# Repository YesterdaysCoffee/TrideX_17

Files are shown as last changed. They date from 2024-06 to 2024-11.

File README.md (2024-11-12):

# TrideX_17
Two headed version of Trident, aka TrideX. Changes include: NEMA 17 steppers for X & Y axis & improved belt assembly.  Generally intended for experienced builders due to lack of step-by-step instructions.  Klipper now supports copy printing for printing two copies at a time, however leveling nozzles can be tricky.  In the future a method to adjust the height of the second head will be added.

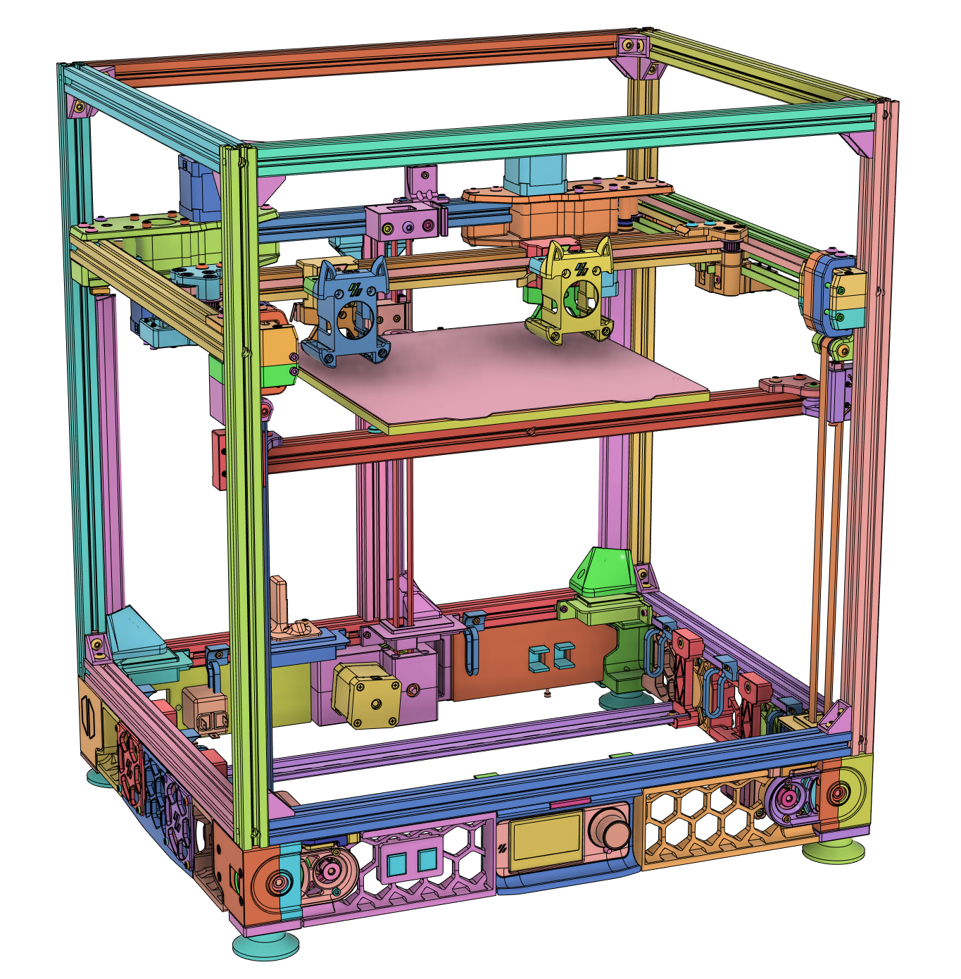
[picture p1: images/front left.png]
Front View.


This is an updated version of TrideX by [eddietheengineer](https://github.com/FrankenVoron/Tridex).

Active development of IDEX macros can be found here: [joseph-greiner's IDEX code](https://github.com/joseph-greiner/tridex_mods/tree/main/printer_configuration)  (as of 2024-7-16).

# Version 0.9
This version uses my favored tool-head, probe, hot-end and end-stop switches.  Depending on popularity and demand, other options can be included (contact me).
Assembly depends on using 3mm and 5mm heat set inserts, some stls have variations using 5mm nuts.  My build used the following and I encourage you to use your favored accessories:
  - Tool-head: Dragon Burner (it is relatively narrow)
  - Bed probe: PCB Klicky, Chartographer 3D being tested
  - Hot-end: Rapido HF, other non-high-flow HE's will likely work
  - End-stops: Mechanical snap switches, Imron D2HW-A201D.
  - Tool-head wiring?  CANbus only (well, maybe USB...)

# 9mm Belts?
Yes, I have started drawing up a gantry using 9mm X/Y belts.  The X linear rail might change.

# Features and Improvements:
  - NEMA 17 steppers for X and Y
  - Belted Z using standard NEMA 17 motors and standard design from VORON Design and MathmaticalPotato, with changes.
  - Improved belt path and belt assembly

# Skirts & Corners:
  - Optional power switch on sides
  - USB port in front skirts
  - LED power switch and dimmer on front skirts, independent from main power switch (warning, I will probably remove this since I was not happy with the results)

  - Electronics bay accessible from the chamber (no more flipping upside down)

# Sizing:
My recommended sizing.  Take your build plate size and:
  - Add 100mm to X (width)
  - Add 50mm to Y (depth)

Typical sizes using square build plates:
  - 200mm, use 250mm sides & 300mm Front/rear, note: electronics bay will be very croweded.
  - 250mm, use 300mm sides & 350mm Front/rear
  - 300mm, use 350mm sides & 400mm Front/rear
  - 350mm, stls have not been included, a 9mm belt version is in the works, and will scale up better.
  - 
A good starting point is a 250mm X 250mm build plate with frame size of 350mm width X 300mm depth.

# Random notes:
- Trident's original Z-drive fits fine, use the original Trident skirts and electronic bay assembly.
- Conversion of a Trident to TrideX-17 has been done. I don't know if the same build plate was used but I'd suggest using a smaller build plate.
- Extra width gives enough space for the idle toolhead to park out if the way.
- Extra depth is needed for the wider X/Y drive assembly and any additional accessories you will use back there. 

In truth any size can be built, it's the skirts which limit frame size options.  Be aware with a very long X-gantry might be problematic.

Frame Size uses standards from Voron Trident: 250, 300 & 350mm with the addition of 400mm for X axis and 200mm on Y axis.  Note, the rear gantry support extrusion is shorter than standard.
Warning: 200mm depth will make fitting electronics a challenge (it didn't work for me).
# Extra Files:
[TridX-17 BOM](https://docs.google.com/spreadsheets/d/e/2PACX-1vSPtPn4Brcn_vidSKCY5Uy1v6KD8oOBtxnAigVPllrFKF_peJibIDPYqSZS3NHdLf7wJWIKfuaN0-26/pubhtml) updated 11-11-2024.

[TridX-17 Change Log](https://docs.google.com/spreadsheets/d/e/2PACX-1vTWaBhZNpjk6NEAdd5VofSHPy5cyr7JOfr-hXRtq54E_nhzI_LgpVOrBIPudIq8-uXfLt_XMnXbr9e0/pubhtml) updated 11-11-2024.

# Notes:
  - Many STL's found here are not compatible with anything else.  The Z-drive, XY-drive assembly and XY joints have all been tweaked for alignment, clearance and assembly.
  - Using a square build plate will be easiest to source.
  - My Firmware files (printer.cfg) are still in development, please depend on [joseph-greiner's IDEX code](https://github.com/joseph-greiner/tridex_mods/tree/main/printer_configuration)
  - Use the CAD file for assembly guidance only, the STL's in the CAD may be out of date.

# To do:
- [] Add folding deck to CAD (piano hinges)
- [] Include detailed description of certain parts, such heat insert size in the BOM
- [] Add assembly tips and tricks
- [] Find micro-adjustable tool-head leveling system

# Got Comments, suggestions, gripes, pizza, praise, flames?  Trolls will be ignored.
Mac McCaskie --> yahoo com (no spaces, you know where to put the punctuation)

Please drop a line if you build this, thanks.

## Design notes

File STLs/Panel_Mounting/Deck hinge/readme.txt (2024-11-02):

Description

Print two halves, slide a 3mm rod in and presto - you have a hinge.

Mix and match lengths to get the desired size.  It's helpful to print in pairs, less confusing that way.

Use double sided tape to attach to surface, VHB tape works well (I think VHB means very high bond, 3M has some and you can find generic VHB).  I don't know if VHB sticks to PLA, let us know in the comments.  VHB works well with ABS.

Optional: Insert a M4 x 4mm machine screw into each end and the hinge pin (that's the 3mm rod) will stay in it's hole.

BOM:

    3mm rod, LOH - 10mm: any metal will work.  I use cheap stainless steel.  I.E. a 60mm hinge will need a 50mm rod.  → LOH = length of hinge.  Tip: A clean end will slide in easier than an end with burrs.
    2 M4 x 4mm screw, any head works fine, IMHO a button head is more aesthetically pleasing.

Settings?  That's pretty much up to you and how strong the hinge needs to be.  A good start point would be:

    Layer: 0.20
    Width: 0.40 
    Walls: 3
    Top & Bottom: 4 

Tip:  Is the rod is too tight? Drill out the holes.  But you say: “I don't have a 3mm drill bit long enough.”  Here's the fix:  Make a D-bit: Get a length of rod and file or grind about 10mm or so flat to the center of the rod.  Try to make the edges you are making sharp, those will be the cutting edges.  The end of the rod will look like a 'D'.  Chuck your new D-bit in a drill and drill that hole out.  Oh, go slow to not heat up the plastic and empty the shavings out often.

https://www.printables.com/model/737250-piano-hinge-expandable-lays-or-hangs-flat-ver2-cor

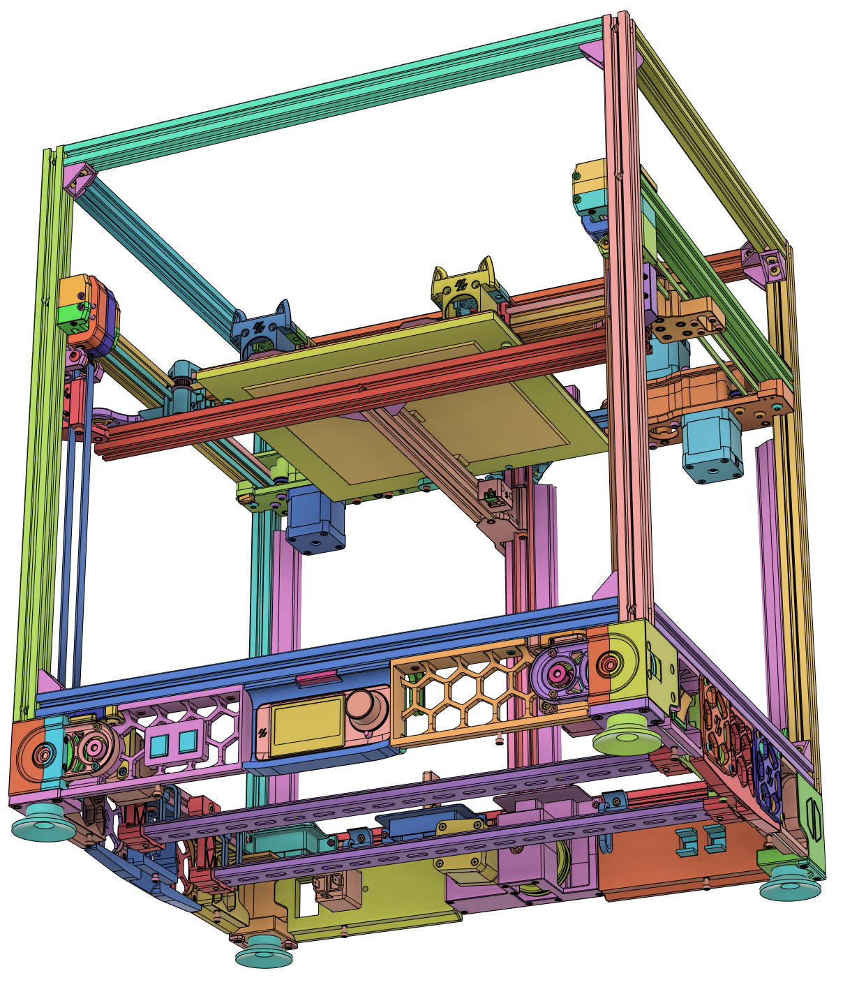
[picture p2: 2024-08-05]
images/front left bottom.png

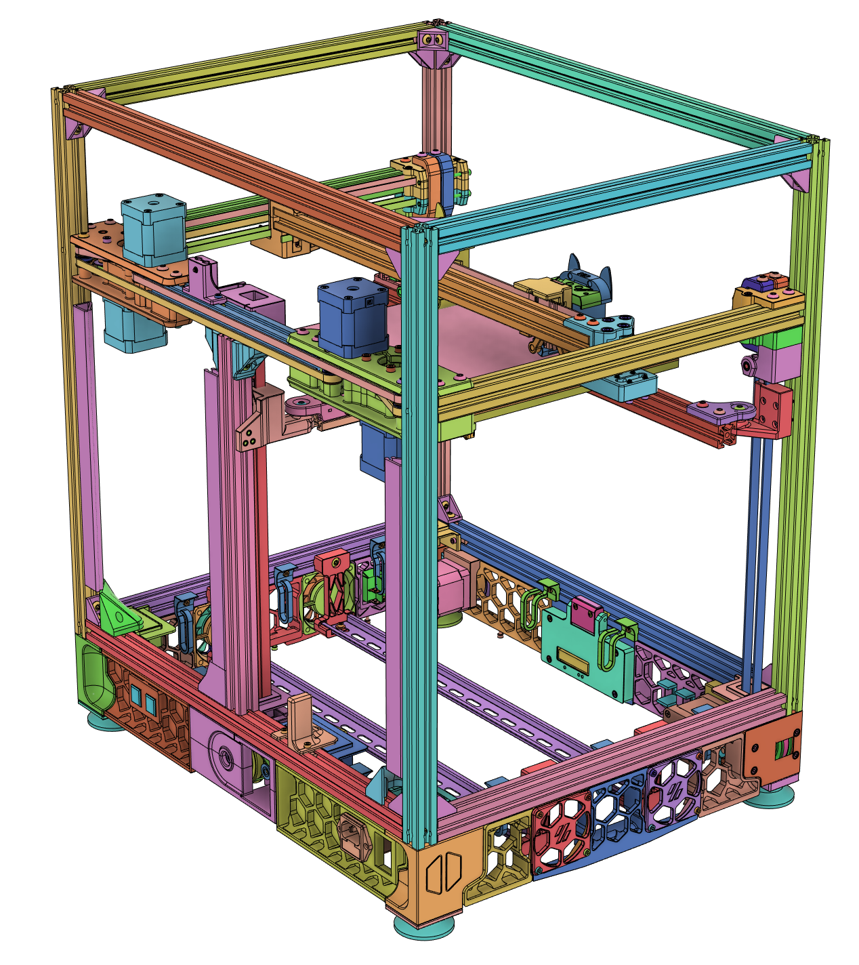
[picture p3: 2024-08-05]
images/back left.png

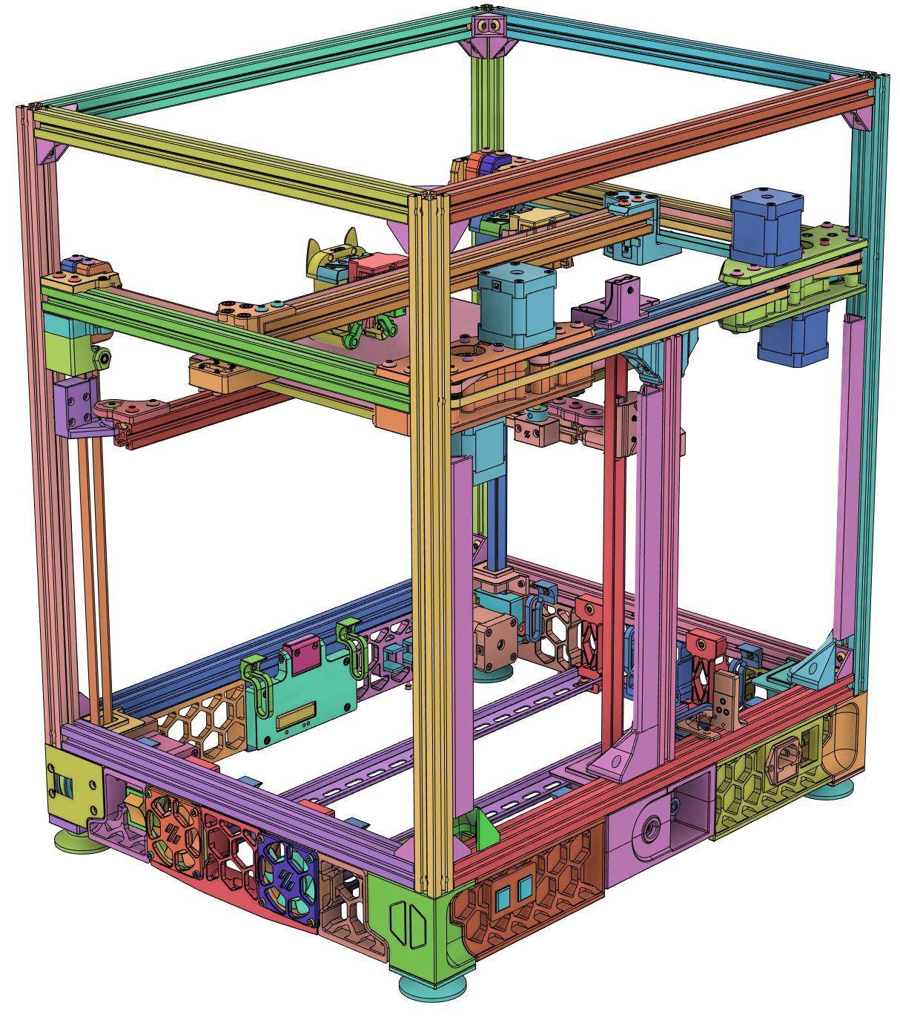
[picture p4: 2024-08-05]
images/front right.png

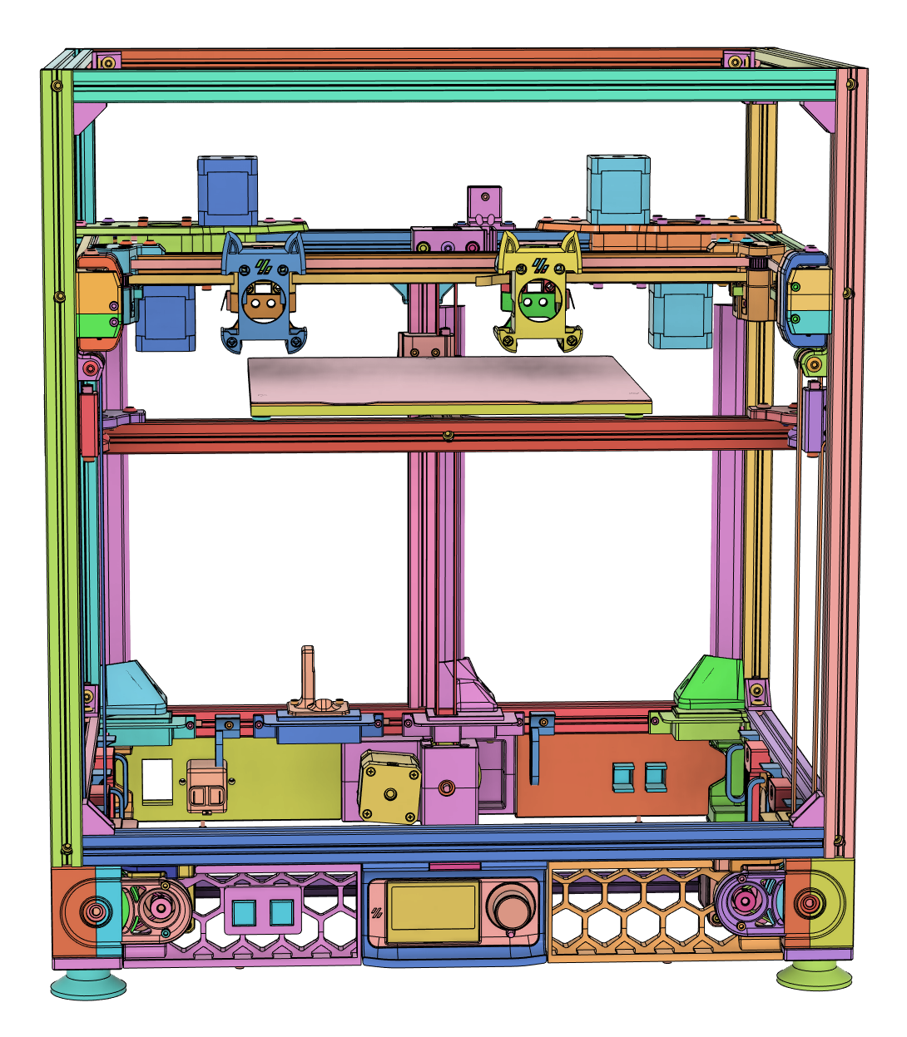
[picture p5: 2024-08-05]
images/front.png

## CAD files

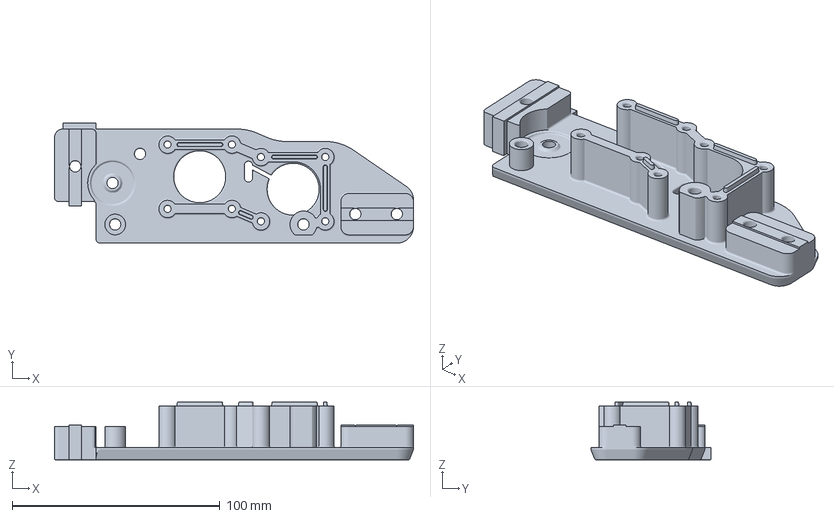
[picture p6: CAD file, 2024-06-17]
STLs/Gantry/XY drive assembly right top/XY drive assembly right bottom.3mf
173.0 x 58.0 x 27.9 mm

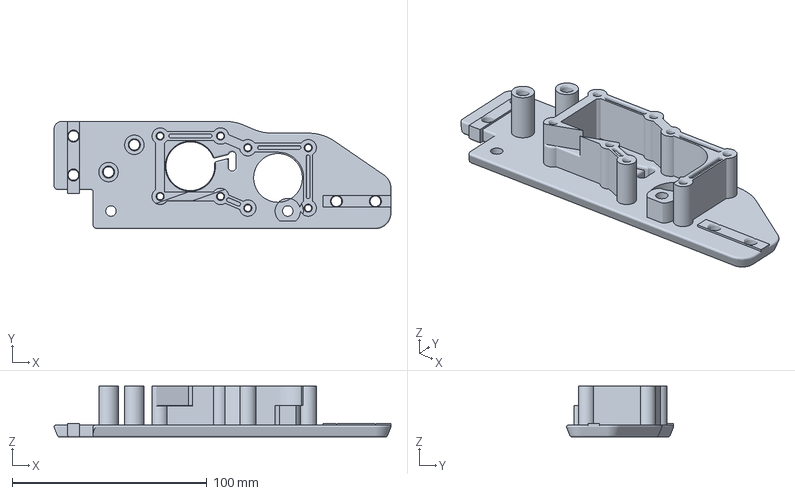
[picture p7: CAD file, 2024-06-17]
STLs/Gantry/XY drive assembly right top/XY drive assembly left top.3mf
173.0 x 55.0 x 26.0 mm

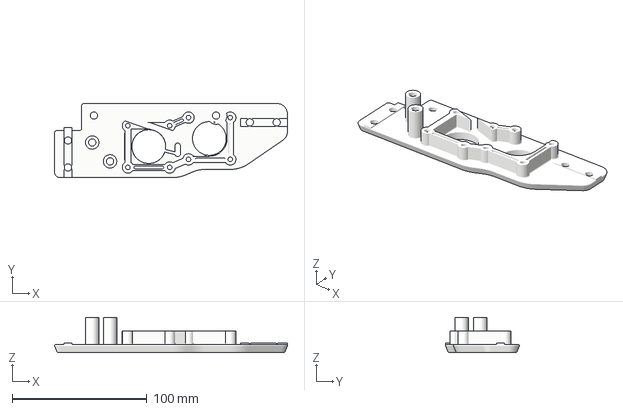
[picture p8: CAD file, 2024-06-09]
STLs/Gantry/XY drive assembly right top/XY drive assembly right top.3mf
173.0 x 55.0 x 26.0 mm

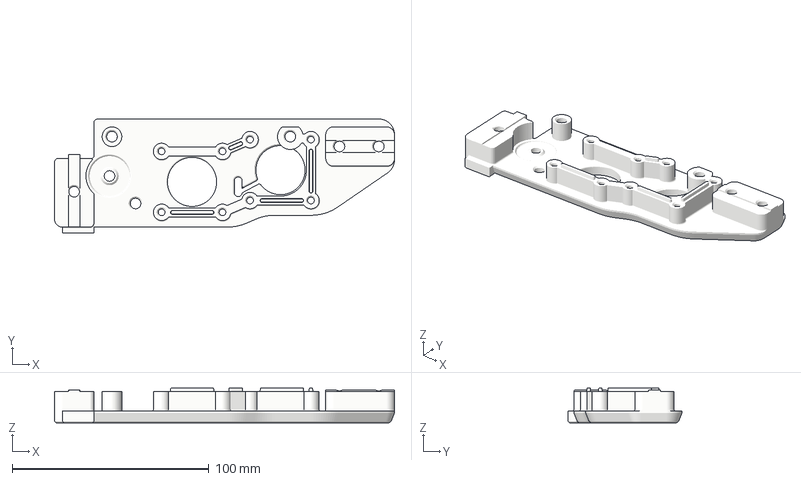
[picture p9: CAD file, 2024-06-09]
STLs/Gantry/XY drive assembly right top/XY drive assembly left bottom.3mf
173.0 x 58.0 x 17.7 mm

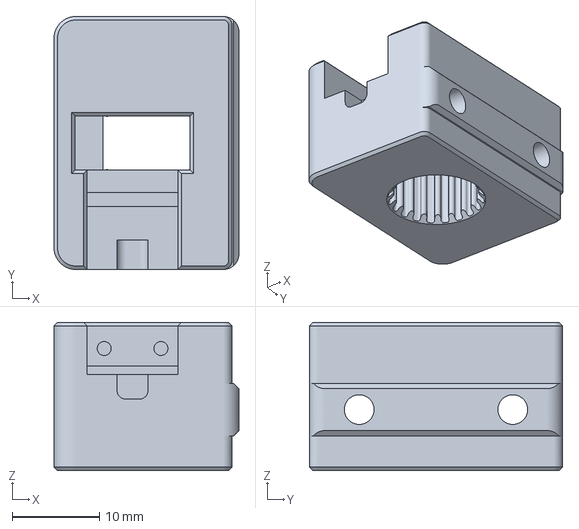
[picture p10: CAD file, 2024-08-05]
STLs/Z_Assembly/Bed/Z Endstop Assembly.3mf
21.2 x 29.0 x 17.0 mm

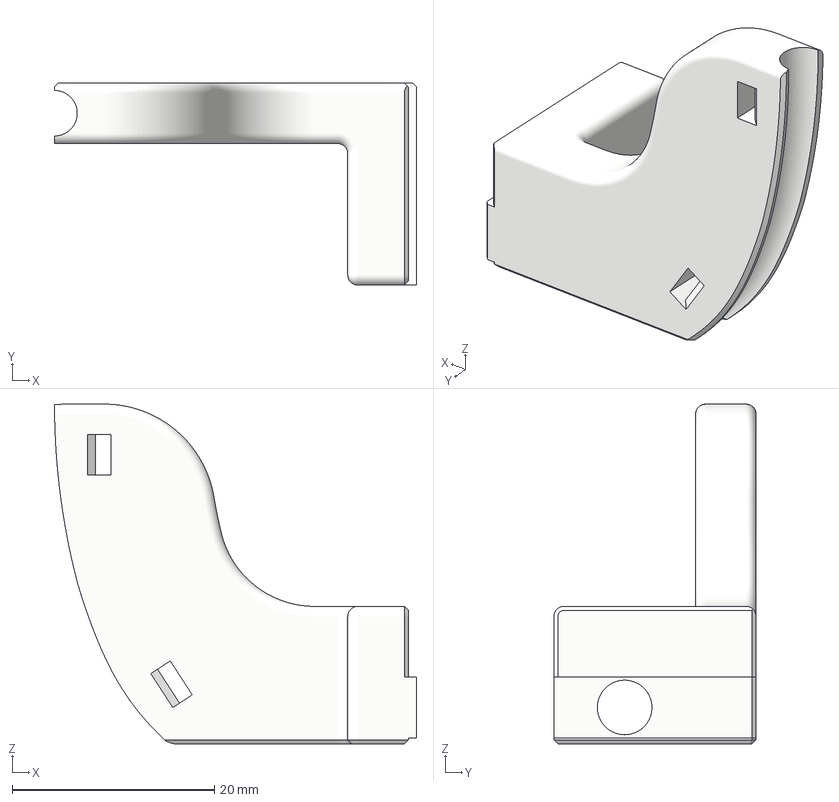
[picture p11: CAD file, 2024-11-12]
STLs/Bowden Tube/bowden tube risor B.3mf
35.8 x 20.0 x 33.6 mm

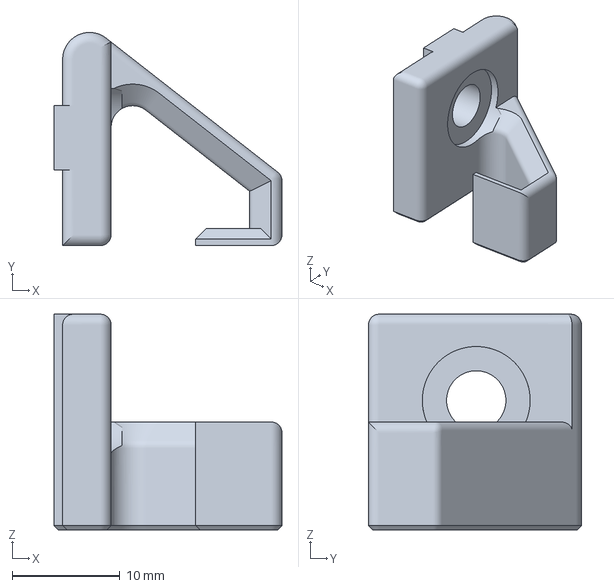
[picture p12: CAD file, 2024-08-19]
STLs/Deck & Wire/Wire channel end right.3mf
21.1 x 19.8 x 20.0 mm

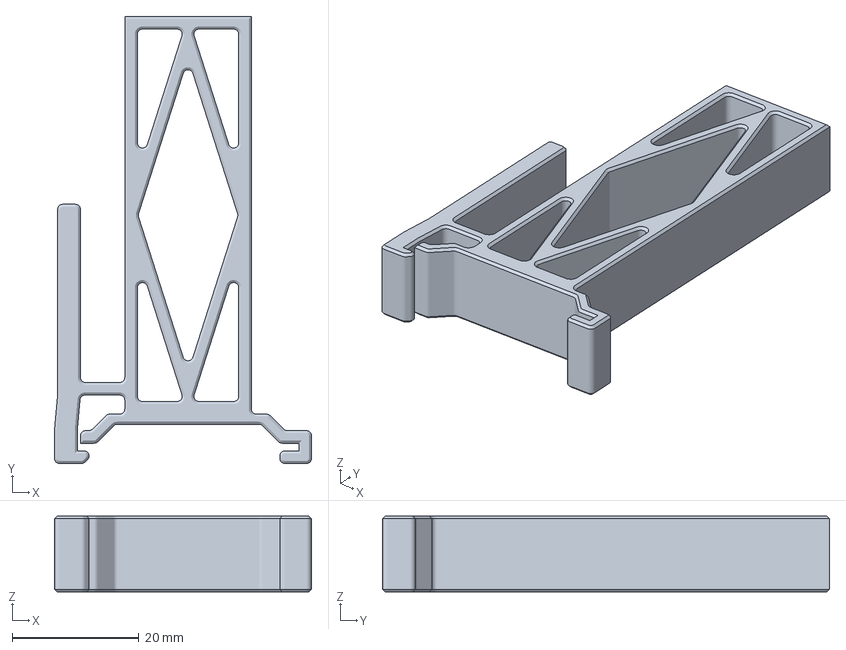
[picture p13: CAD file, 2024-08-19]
STLs/Electronics Bay/DIN 3 fixtures/Deck support post x2.3mf
40.6 x 70.6 x 12.0 mm

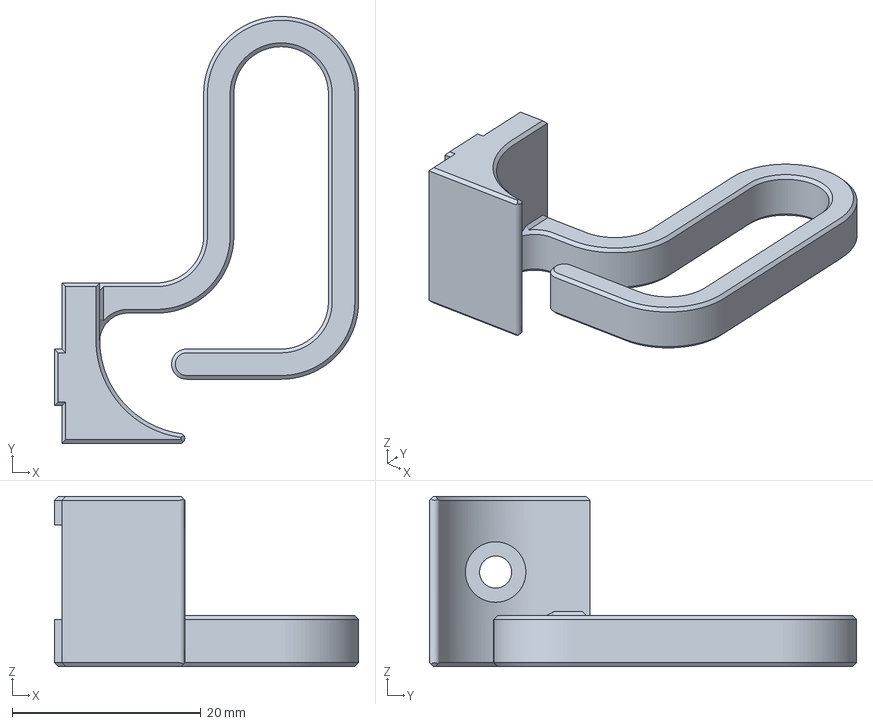
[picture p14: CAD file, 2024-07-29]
STLs/Electronics Bay/wire hanger & deck support B.3mf
32.2 x 45.2 x 18.0 mm

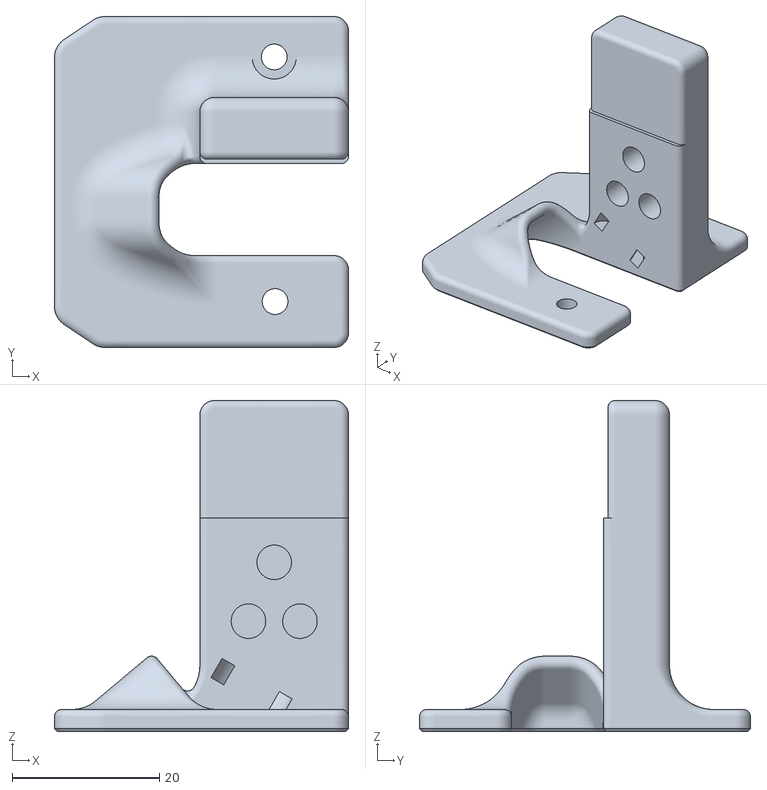
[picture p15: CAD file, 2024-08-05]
STLs/Frame/z_cable_chain_mount_3hole.stl
40.0 x 45.0 x 45.0

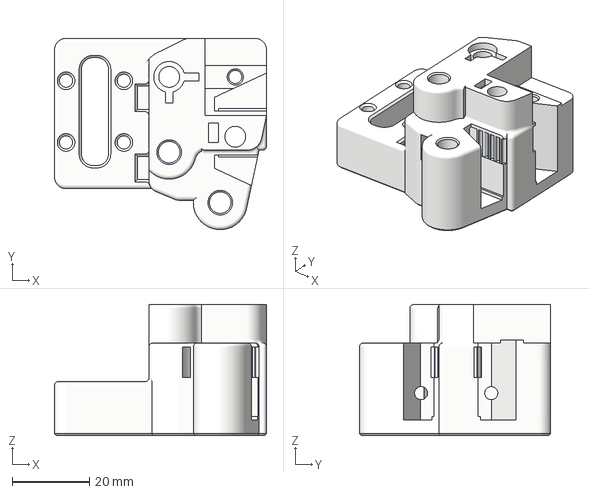
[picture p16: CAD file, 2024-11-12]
STLs/Gantry/XY_Joints/XY joint left bottom v2.3mf
55.0 x 49.6 x 34.0 mm

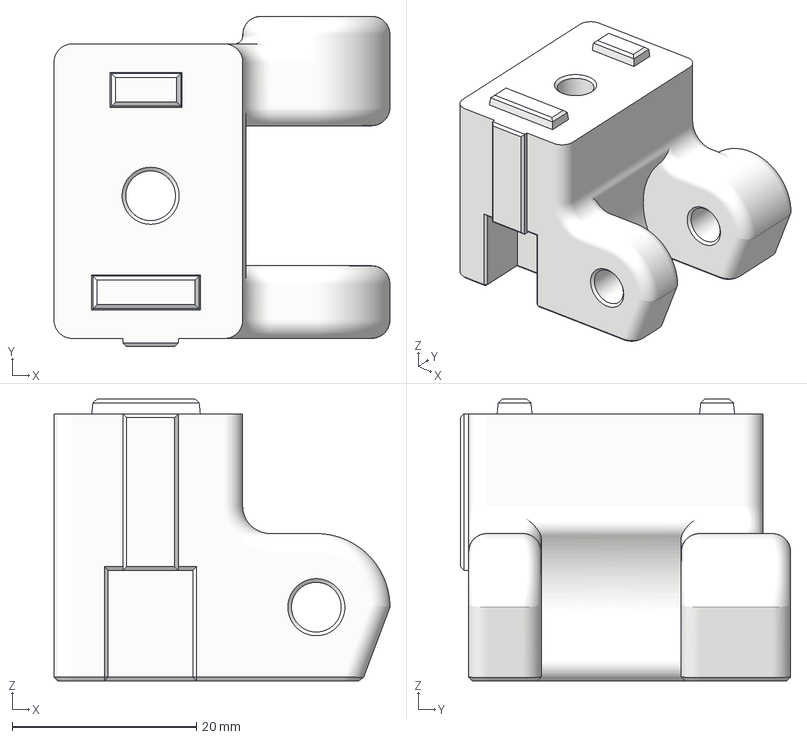
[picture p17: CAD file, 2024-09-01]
STLs/Idlers/Z Idler left.3mf
36.5 x 35.9 x 30.6 mm

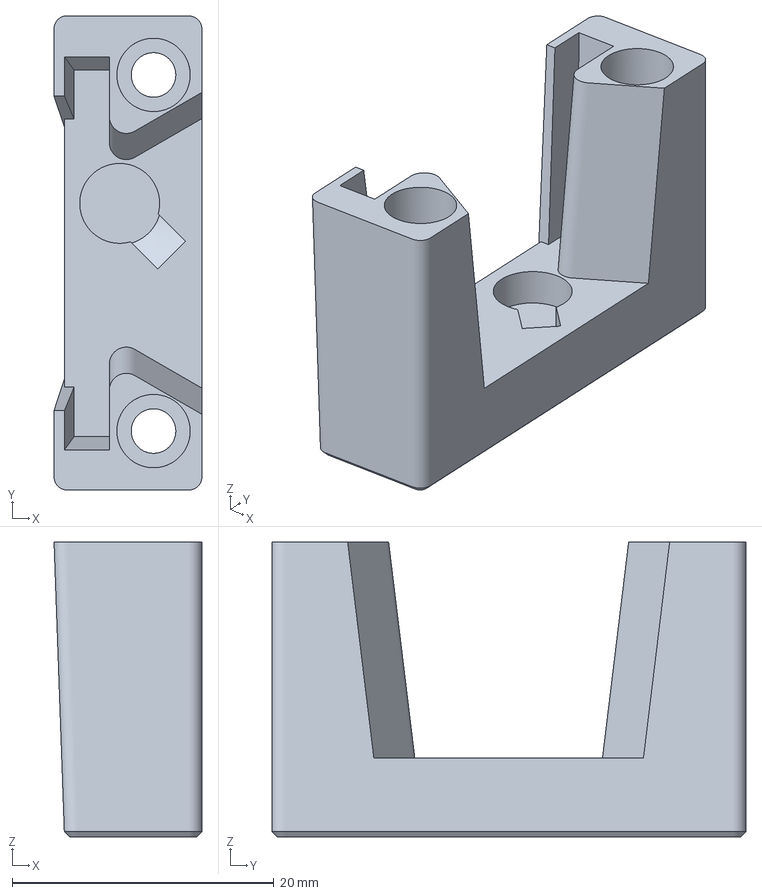
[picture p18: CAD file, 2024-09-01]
STLs/Klicky/bigger probe dock with hood.3mf
11.3 x 36.2 x 22.5 mm

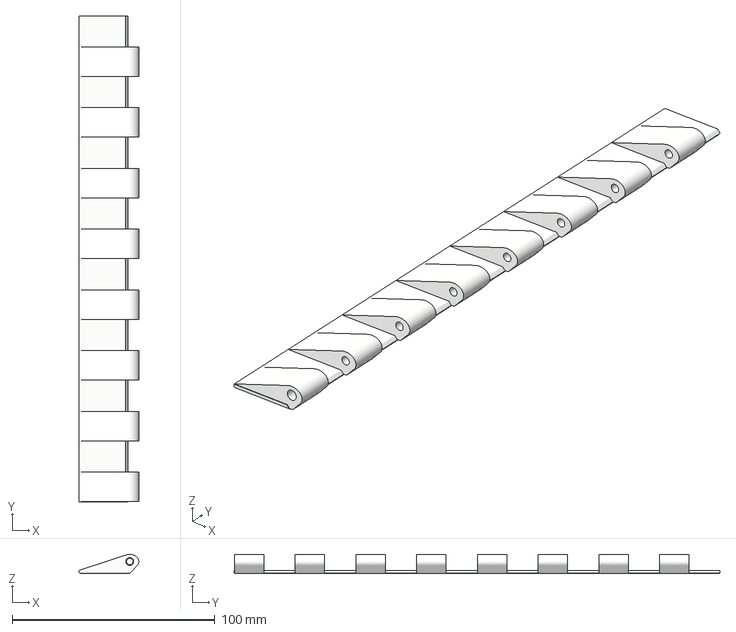
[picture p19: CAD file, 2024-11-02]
STLs/Panel_Mounting/Deck hinge/240mm Half Hinge v2.3mf
29.5 x 240.0 x 9.50 mm

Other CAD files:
STLs/Panel_Mounting/Front_Doors/my Side Hinge v3.3mf
STLs/Skirts/(a) LED switch panel small v2.3mf
STLs/Skirts/200/side skirt A 200 pwr switch.3mf
STLs/Skirts/250/cam base mount.3mf
STLs/Bowden Tube/bowden clamp 50deg plug 4mm mirror.3mf
STLs/Bowden Tube/bowden clamp 50deg plug 4mm.3mf
STLs/Bowden Tube/bowden clamp 50deg strap 4mm mirror.3mf
STLs/Bowden Tube/bowden clamp 50deg strap 4mm.3mf
STLs/Bowden Tube/bowden clamp 60deg plug 4mm mirror.3mf
STLs/Bowden Tube/bowden clamp 60deg plug 4mm.3mf
STLs/Bowden Tube/bowden clamp 60deg strap 4mm mirror.3mf
STLs/Bowden Tube/bowden clamp 60deg strap 4mm.3mf
STLs/Bowden Tube/bowden clamp 75deg plug 4mm mirror.3mf
STLs/Bowden Tube/bowden clamp 75deg plug 4mm.3mf
STLs/Bowden Tube/bowden clamp 75deg strap 4mm mirror.3mf
STLs/Bowden Tube/bowden clamp 75deg strap 4mm.3mf
STLs/Bowden Tube/bowden clamp 90deg plug 4mm.3mf
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

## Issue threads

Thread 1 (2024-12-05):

Can I use the motor mounts you designed on the original design?

scshsy, 2024-12-05:
I am planning to build a Tridex model, referencing https://github.com/FrankenVoron/Tridex. However, it uses NEMA14 motors for the X and Y axes, which is a concern for me. I have a lot of NEMA17 motors on hand, and we don't want to waste them. After searching, I found your project, which is excellent. Could you please let me know if the motor mounts for the X and Y axes can be directly used on the FrankenVoron/Tridex machine? Regardless of whether it is possible, thank you very much. Additionally, if it is possible to use them, do I need to slightly extend the X and Y axis profiles to ensure the print area is not affected, since the motors take up more space in the X and Y directions? Thank you again.

YesterdaysCoffee, 2024-12-05:
No, the belts will not line up.
However, the lead screws used in trident and tridex are compatible and will replace the belted z drive.
    On Thursday, December 5, 2024 at 07:12:08 AM CST, 火龙果 ***@***.***> wrote:

I am planning to build a Tridex model, referencing https://github.com/FrankenVoron/Tridex. However, it uses NEMA14 motors for the X and Y axes, which is a concern for me. I have a lot of NEMA17 motors on hand, and we don't want to waste them. After searching, I found your project, which is excellent. Could you please let me know if the motor mounts for the X and Y axes can be directly used on the FrankenVoron/Tridex machine? Regardless of whether it is possible, thank you very much. Additionally, if it is possible to use them, do I need to slightly extend the X and Y axis profiles to ensure the print area is not affected, since the motors take up more space in the X and Y directions? Thank you again.

—
Reply to this email directly, view it on GitHub, or unsubscribe.
You are receiving this because you are subscribed to this thread.Message ID: ***@***.***>

scshsy, 2024-12-06:
Thank you for your response. When you mentioned that the belts cannot be aligned, are you referring to the vertical direction?

YesterdaysCoffee, 2024-12-06:
I needed to move the bearing stacks and idlers for the XY drive assembly to use NEMA 17 motors.  Those belts run horizontally and probably will not work with original front idlers or XY joints.
The Z belts run vertically.  The original lead screw steppers will work well if you do not want to use the new belted Z assembly.

regards,mac
    On Thursday, December 5, 2024 at 08:03:20 PM CST, 火龙果 ***@***.***> wrote:

Thank you for your response. When you mentioned that the belts cannot be aligned, are you referring to the vertical direction?

—
Reply to this email directly, view it on GitHub, or unsubscribe.
You are receiving this because you commented.Message ID: ***@***.***>

scshsy, 2024-12-07:
Thank you, I saw someone use your XY motor base on YouTube, https://www.youtube.com/watch?v=F_DXAhIZfbw&t=35s, so there should be no problem. I am preparing to give it a try. Thank you again.

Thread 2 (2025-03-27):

Some advices

pasha4ur, 2025-03-27:
Hello.

- The print bed will fall when you turn off the power on the Z motors. A worm gear or a planetary gear can help.
- These X/Y tensioners are unreliable. Can you try to make something like BFI?
- Try to replace screws in the x/y joints with pin mod.
- You can make support of the x, y and u motors' shafts with the help of the F695 bearing. I made this improvement with my trident:

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

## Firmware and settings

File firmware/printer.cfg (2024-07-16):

# printer.cfg
[include mainsail.cfg]
[include Toolhead_LEDs.cfg]   #originally: stealthburner_leds.cfg
[include toolheads.cfg]
[include macros_basic.cfg]   #moved from printer.cfg
[include macros_IDEX.cfg]    #originally: IDEX_mode.cfg
[include klicky-macros.cfg]

[mcu]
##  Obtain definition by "ls -l /dev/serial/by-id/" then unplug to verify
serial: /dev/serial/by-id/usb-Klipper_stm32f446xx_2A0035000951313133353932-if00
restart_method: command #rpi_usb #command

[virtual_sdcard]
path: /home/macmc/printer_data/gcodes
on_error_gcode: CANCEL_PRINT

[printer]
kinematics: hybrid_corexy
max_velocity: 300
max_accel: 4000
max_z_velocity: 25
max_z_accel: 350

[idle_timeout]
timeout: 1800

[resonance_tester]
accel_chip: adxl345 tool0
probe_points:
    125, 125, 50                    # 150, 150, 50 for 300 Trident

[probe]
pin: tool0:PB8
x_offset: 1
y_offset: 27.0
z_offset = 2.0
speed: 3
lift_speed: 10
samples:5
samples_result: median
sample_retract_dist: 2.0
samples_tolerance: 0.01
samples_tolerance_retries: 5

# X Steppers ################################################################################

[stepper_x] 
# controls toolhead 0 (T0) 
# motor0/driver0: left toolhead -right X stepper
enable_pin: !PF14
step_pin: PF13
dir_pin: PF12
microsteps: 32
rotation_distance: 40
endstop_pin: ^tool0:PB9
position_min: -50
position_endstop: -50
position_max: 250
homing_speed: 60
homing_retract_dist: 5
second_homing_speed: 3

[tmc2209 stepper_x]
uart_pin: PC4
interpolate: false
run_current: 0.8
sense_resistor: 0.110
stealthchop_threshold: 0

[dual_carriage]  #(stepper_x1)
# controls toolhead 1 (T1)
# motor1/driver1: right toolhead -left X stepper
axis: x
safe_distance: 35 #Set to width of your tool head
enable_pin: !PF15
step_pin: PG0
dir_pin: PG1
microsteps: 32
rotation_distance: 40
endstop_pin: ^tool1:PB9
position_min: 8
position_endstop:301.6
position_max: 301.6
homing_speed: 60
homing_retract_dist: 5
second_homing_speed: 3


[tmc2209 dual_carriage]
uart_pin: PD11
interpolate: false
run_current: 0.8
sense_resistor: 0.110
stealthchop_threshold: 0

# Y Steppers ################################################################################

[stepper_y]
# motor 2_1, driver 2, left Y stepper
enable_pin: !PG5
step_pin: PF11
dir_pin: PG3
microsteps: 32
rotation_distance: 40
endstop_pin: PG9
position_endstop: 243
position_max: 243
position_min: 0
homing_speed: 60
second_homing_speed: 5
homing_retract_dist: 5

[tmc2209 stepper_y]
uart_pin: PC6
interpolate: false
run_current: 0.8
sense_resistor: 0.110
stealthchop_threshold: 0

[stepper_y1]
# motor3/driver3; right Y stepper
enable_pin: !PA0
step_pin: PG4
dir_pin: !PC1
microsteps: 32
rotation_distance: 40
#full_steps_per_rotation:200 

[tmc2209 stepper_y1]
uart_pin: PC7
interpolate: false
run_current: 0.8
sense_resistor: 0.110
stealthchop_threshold: 0

# Z Steppers ################################################################################

[stepper_z]
#motor4/driver4; front left Z
enable_pin: !PG2
step_pin: PF9
dir_pin: PF10
microsteps: 32
rotation_distance: 40
gear_ratio: 80:16
endstop_pin: probe:z_virtual_endstop
position_max: 250
position_min: -5
homing_speed: 3          # 10 is recommended maximum.  3 is gentle on klicky and switchs last longer
second_homing_speed: 2
homing_retract_speed: 10
homing_retract_dist: 2

[tmc2209 stepper_z]
uart_pin: PF2
run_current: 0.8
sense_resistor: 0.110
stealthchop_threshold: 0

[stepper_z1]
#motor5/driver5; rear Z
enable_pin: !PF1
step_pin: PC13
dir_pin: !PF0
microsteps: 32
rotation_distance: 40
gear_ratio: 80:16

[tmc2209 stepper_z1]
uart_pin: PE4
interpolate: False
run_current: 0.8
sense_resistor: 0.110
stealthchop_threshold: 0

[stepper_z2]
#motor6/driver6; front right Z
enable_pin: !PD4
step_pin: PE2
dir_pin: !PE3
microsteps: 32
rotation_distance: 40
gear_ratio: 80:16

[tmc2209 stepper_z2]
uart_pin: PE1
interpolate: False
run_current: 0.8
sense_resistor: 0.110
stealthchop_threshold: 0

#   Extruder PID - in printer.cfg so save_config works properly ################################################################################

[extruder]
## PID control extruder, tune this
control: pid
pid_Kp: 36.965
pid_Ki: 4.650
pid_Kd: 73.468

[extruder1]
## PID control extruder1, tune this
control: pid
pid_Kp: 35.650
pid_Ki: 4.850
pid_Kd: 65.508

# Bed ################################################################################

[heater_bed]
heater_pin: PA3
sensor_type: Generic 3950
sensor_pin: PF3
max_power: 0.80 
min_temp: 0
max_temp: 120
pwm_cycle_time: 0.016
control: pid
pid_kp: 14.810
pid_ki: 0.914
pid_kd: 59.983

[z_tilt]
##  Use Z_TILT_ADJUST to level the bed .
z_positions:
    -100, 22    
    125, 298
    350, 22
points:
    10, 10
    125, 220
    240, 10
speed: 200
horizontal_move_z: 15
retries: 5
retry_tolerance: 0.0075

# Sensors and Extras ################################################################################

[controller_fan BayFan0]
#FAN 0 - electronics bay
pin: PA8
max_power: 0.70
kick_start_time: 0.5
stepper: stepper_z, stepper_x, stepper_y

##  [controller_fan controller_fan1]
##  pin: PD15
##  max_power: 0.5
##  kick_start_time: 0.5
##  heater: heater_bed

[temperature_sensor raspberry_pi]
sensor_type: temperature_host
gcode_id: D
min_temp: 0
max_temp: 100

#[temperature_sensor chamber]
#sensor_type: Generic 3950
#sensor_pin: head1:PA1
#pullup_resistor: 2200
#min_temp: -100
#max_temp: 100
#gcode_id: C

# 	Display & Lighting ################################################################################

##  mini12864 LCD Display
[display]
lcd_type: uc1701
cs_pin: PE9
a0_pin: PE10
rst_pin: PE12
encoder_pins: ^PB2, ^PB1
click_pin: ^!PE7
contrast: 63
spi_software_miso_pin: PA6
spi_software_mosi_pin: PA7
spi_software_sclk_pin: PA5

##  control Neopixel RGB in mini12864 display
[neopixel btt_mini12864]
pin: PE13
chain_count: 3
initial_RED: 0.9
initial_GREEN: 0.0
initial_BLUE: 0.0
color_order: RGB

##  Set RGB values on boot up for each Neopixel. 
##  Index 1 = display, Index 2 and 3 = Knob
[delayed_gcode setdisplayneopixel]
initial_duration: 1
gcode:
  SET_LED LED=btt_mini12864 RED=0.0431 GREEN=0.9216 BLUE=0.0196 INDEX=3 TRANSMIT=1
  SET_LED LED=btt_mini12864 RED=1 GREEN=0 BLUE=0 INDEX=2 TRANSMIT=0
  SET_LED LED=btt_mini12864 RED=0 GREEN=0 BLUE=1 INDEX=1

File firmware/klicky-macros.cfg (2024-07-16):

# klicky-macros.cfg
# This macro was provided by discord user Garrettwp to whom i give my thanks for sharing it with me.
# I have tweaked it a lot.
# They are based on the great Annex magprobe dockable probe macros "#Originally developed by Mental,
# modified for better use on K-series printers by RyanG and Trails", kudos to them.
# That macro as since evolved into a klipper plugin that currently is pending inclusion in klipper,
# more information here, https://github.com/Annex-Engineering/Quickdraw_Probe/tree/main/Klipper_Macros
# User richardjm revised the macro variables and added some functions
# User sporkus added led status notifications
# Thanks to all who helped,
# by standing on the shoulders of giants, lets see if we can see further
#
# the current home for this version is https://github.com/jlas1/Klicky-Probe
[include klicky-variables.cfg]
[respond]

[gcode_macro _Probe_Variables]
variable_probe_attached:            False
variable_probe_state:               False
variable_probe_lock:                False
variable_probe_z_homed:             False
variable_z_endstop_x:               0
variable_z_endstop_y:               0
gcode:

# from: klicky-z-tilt-adjust.cfg
###################
## Z Tilt Adjust
[gcode_macro Z_TILT_ADJUST]
rename_existing: _Z_TILT_ADJUST
description:
gcode:
    {% set V = printer["gcode_macro _User_Variables"].verbose %}
    {% if V %}
        { action_respond_info("Z Tilt Adjust") }
    {% endif %}

    _CheckProbe action=query
	G90
    Attach_Probe
    _KLICKY_STATUS_LEVELING

    _Z_TILT_ADJUST {% for p in params
          %}{'%s=%s ' % (p, params[p])}{%
         endfor %}
    Dock_Probe
    G28 Z0
    
#checks if the variable definitions are up to date
[gcode_macro _klicky_check_variables_version]
gcode:
    {% set version = printer["gcode_macro _User_Variables"].version|default(0) %}

    {% if version != 1 %}
        { action_raise_error("Please update your klicky variables, there are some functionality changes") }
    {% endif %}

[gcode_macro _KlickyDebug]
gcode:
    {% set message  = params.MSG %}
    {% set debug = printer["gcode_macro _User_Variables"].debug|default(False) %}

    {% if debug %}
        { action_respond_info(message) }
    {% endif %}


[gcode_macro _exit_point]
gcode:
    {% set function  = 'pre_' ~ params.FUNCTION %}
    {% set move  = params.MOVE|default(0) %}
    {% set speed = printer["gcode_macro _User_Variables"].travel_speed %}

    # mandatory to save the new safe position
    M400
    SET_VELOCITY_LIMIT ACCEL={printer.configfile.settings.printer.max_accel}
    RESTORE_GCODE_STATE NAME={function} MOVE={move} MOVE_SPEED={speed}


[gcode_macro _entry_point]
gcode:
    {% set function  = 'pre_' ~ params.FUNCTION %}
    {% set move_accel = printer["gcode_macro _User_Variables"].move_accel|default(1000) %}
    # mandatory to save the new safe position
    M400
    SAVE_GCODE_STATE NAME={function}
    # removes the Z offset for better bed based docking
    SET_GCODE_OFFSET Z=0
    # all the macros initially assume absolute positioning
    G90
    # set a safe(sane) Acceleration
    SET_VELOCITY_LIMIT ACCEL={move_accel}

[gcode_macro _Homing_Variables]
gcode:
    {% set reset  = params.RESET|default(0) %}
    {% if reset %}
        SET_GCODE_VARIABLE MACRO=_Probe_Variables VARIABLE=probe_lock VALUE={ False }
    {% endif %}

##########################
# Attach probe and lock it
[gcode_macro Attach_Probe_Lock]
description: Attaches Klicky Probe, can only be docked after unlocking
gcode:
    Attach_Probe
    _Probe_Lock

########################
# Dock probe and lock it
[gcode_macro Dock_Probe_Unlock]
description: Docks Klicky Probe even if it was locked
gcode:
    _Probe_Unlock
    Dock_Probe

##############
# Unlock Probe
[gcode_macro _Probe_Unlock]
description: Unlocks Klicky Probe state
gcode:
    _KlickyDebug msg="_Probe_Lock setting probe_lock variable to False"
    SET_GCODE_VARIABLE MACRO=_Probe_Variables VARIABLE=probe_lock VALUE={ False }

############
# Lock Probe
[gcode_macro _Probe_Lock]
description: Locks Klicky Probe state
gcode:
    _KlickyDebug msg="_Probe_Lock setting probe_lock variable to True"
    SET_GCODE_VARIABLE MACRO=_Probe_Variables VARIABLE=probe_lock VALUE={ True }

###################
# Klicky Dock Servo Deploy

[gcode_macro _DeployKlickyDock]
description: Deploys Klicky servo-controlled dock
gcode:
    {% set enable_dock_servo = printer["gcode_macro _User_Variables"].enable_dock_servo|default(False) %}
    {% set servo_delay = printer["gcode_macro _User_Variables"].servo_delay|default(1000) %}
    {% set servo_name = printer["gcode_macro _User_Variables"].servo_name %}
    {% set servo_deploy = printer["gcode_macro _User_Variables"].servo_deploy|default(360) %}

    #wait for all the moves to complete
    M400
    {% if enable_dock_servo != False %}
        _KlickyDebug msg="_DeployKlickyDock Klicky servo configuration enabled"
        {% if servo_deploy == 360 %}
            { action_raise_error("Klicky: servo active on klicky-variables, but no servo deploy angle specified") }
        {% endif %}
        _KlickyDebug msg="_DeployKlickyDock SET_SERVO SERVO={servo_name|string} ANGLE={servo_deploy|int}"
        SET_SERVO SERVO={servo_name|string} ANGLE={servo_deploy|int}
        M400
        G4 P{servo_delay|int}
        _KlickyDebug msg="_DeployKlickyDock SET_SERVO SERVO={servo_name|string} WIDTH=0"
        SET_SERVO SERVO={servo_name|string} WIDTH=0
    {% elif printer["gcode_macro _DeployDock"] is defined %}
        _KlickyDebug msg="_DeployKlickyDock calling _DeployDock"
        _DeployDock
    {% endif %}

####################
# Dock Servo Retract

[gcode_macro _RetractKlickyDock]
description: Retracts Klicky servo-controlled dock
gcode:
    {% set enable_dock_servo = printer["gcode_macro _User_Variables"].enable_dock_servo|default(False) %}
    {% set servo_delay = printer["gcode_macro _User_Variables"].servo_delay|default(1000) %}
    {% set servo_name = printer["gcode_macro _User_Variables"].servo_name %}
    {% set servo_retract = printer["gcode_macro _User_Variables"].servo_retract|default(360) %}

    #wait for all the moves to complete
    M400
    {% if enable_dock_servo != False %}
        _KlickyDebug msg="_RetractKlickyDock Klicky servo configuration enabled"
        {% if servo_retract == 360 %}
            { action_raise_error("Klicky: servo active on klicky-variables, but no servo retract angle specified") }
        {% endif %}
        _KlickyDebug msg="_RetractKlickyDock SET_SERVO SERVO={servo_name|string} ANGLE={servo_retract|int}"
        SET_SERVO SERVO={servo_name|string} ANGLE={servo_retract|int}
        M400
        G4 P{servo_delay|int}
        _KlickyDebug msg="_RetractKlickyDock SET_SERVO SERVO={servo_name|string} WIDTH=0"
        SET_SERVO SERVO={servo_name|string} WIDTH=0
    {% elif printer["gcode_macro _RetractDock"] is defined %}
        _KlickyDebug msg="_RetractKlickyDock calling _RetractDock"
        _RetractDock
    {% endif %}
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

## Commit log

2024-04-15 upsie 2
    [(a) LED switch panel large.3mf, (a) LED switch panel small.3mf, (a) front idler tensioner left X.3mf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]
2024-05-16 big upload, files are closer to being done-done.
    [(a) Z-Carriage_belt_tensioner-x3.3mf, (a) Z-drive left Base Plate 5mm HS.3mf, (a) Z-drive left Base Plate.3mf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]
2024-05-16 adjustment of wiring pass through in XY drive assembly
    [XY drive assembly left bottom.3mf, XY drive assembly left top.3mf, XY drive assembly right bottom.3mf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]
2024-06-09 more adjustments and tweeks
    [(a) Keysone blank.3mf, Carriage_Base_EndStop_dragon burner klicky.3mf, Carriage_Mount Dragon Burner A.3mf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]
2024-06-17 rotating objects into correct (intended) printable position
    [(a) Keysone blank.3mf, (a) LED switch panel large.3mf, (a) LED switch panel small.3mf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]
2024-07-16 Assembly Guide, various tweeks and fix's
    [(a) LED switch panel small v2.3mf, (a) Z-Carriage_belt_tensioner-x3.3mf, (a) Z-drive right Base Plate.3mf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]
2024-07-16 minor update
    [Bed_carriage_rear_2hole_5mm_HS.3mf, Carriage_Mount Dragon Burner Left.3mf, Carriage_Mount Dragon Burner right.3mf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]
2024-07-18 CAD Update, rear bed carriage rework
    [Bed_carriage_rear_2hole.3mf, Bed_carriage_rear_2hole_5mm_HS.3mf, Bed_carriage_rear_3hole.3mf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]
2024-07-29 Deck cutouts & electronics bay additions
    [(a) Z-Carriage_belt_tensioner-x3.3mf, 10x11 Chain Z.f3d, Bed_Frame_mount_rear_alt.3mf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]
2024-08-05 wiring fixtures additions
    [(a) front idler tensioner left X.3mf, (a) front idler tensioner left Y.3mf, (a) front idler tensioner right X.3mf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]
2024-08-10 add wire conduits, moved bed frame mounts
    [10x11 Chain Z.f3d, Bed frame mount left.3mf, Bed frame mount rear.3mf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]
2024-08-11 quick adjustment
    [Bed frame mount left.3mf, Bed frame mount rear.3mf, Bed frame mount right.3mf]
2024-08-19 wire conduits added, z belt path tweak
    [Bed carriage left 5mm HS.3mf, Bed carriage left.3mf, Bed carriage rear 2 hole.3mf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]
2024-09-01 Adding optional Bed mount, Types A & B, and slight adjustment of z belt path
    Bed mount now has two options, Type A is my original, Type B gains approx 15mm of travel,
    [Bed carriage left 5mm HS.3mf, Bed carriage left.3mf, Bed carriage rear 2 hole.3mf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]
2024-09-02 updating CAD, type A & B bed-carriage assemblies
2024-11-02 Add deck hinge, skirts with USB panel, Carto mount, etc
    [120mm Half Hinge v2.3mf, 150mm Half Hinge v2.3mf, 180mm Half Hinge v2.3mf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]
2024-11-03 Add bowden tube clamp
    [bowden clamp 50deg plug 4mm mirror.3mf, bowden clamp 50deg plug 4mm.3mf, bowden clamp 50deg strap 4mm mirror.3mf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]
2024-11-12 fixing XY joints
    [XY joint left bottom v2.3mf, XY joint left top v2.3mf, XY joint right bottom v2.3mf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]
2024-11-12 updated CAD
